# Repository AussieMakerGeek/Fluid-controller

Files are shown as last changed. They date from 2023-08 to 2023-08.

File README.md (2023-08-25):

# Fluid-controller
This is a fork of the original Fluid controller but it only retains handfulls of code and implements simple features for controlling my Gravoraph LS800 Co2 Laser that I converted using an MKS-Tinybee 

# Main functions
My implementation uses STM32 Bluepill over direct serial with the MKS-Tinybee using the new secondary serial function in FluidNC. I use the wifi function so bluetooth is not ideal for me, plus I can build this into my machine, no batteries etc.

# Display shows 
Machine coordinates, Work coordinates, Machine status, jog distance and whether X/Y jog or Z jog is active.  Since my machine has a visible laser, I also added a display for it's status.

Main functions of buttons: 
Home, Home Z, Unlock/Reset, Visible laser, Jog distance +, Jog distance -, directional buttons and Z/XY toggle.

No menus...

# Hardware
1. STM32 Bluepill (128k used, about 50% free)
2. ILI9341 based 2.5" display (320x240 res)
3. 11 X TTP223 Touch buttons - The Pad 'A' will need to be shorted to make them active LOW.

# Wiring
The buttons and display were directly wired to the Bluepill, no need for PCB. Mounted in a 3d Printed panel for install to the machine.

# Programming
Programming is done in Arduino IDE. All code exists in one single file. Button definitions set out the pins used.  

Project uses the TFT_eSPI library which requires setting the display parameters in user_setup.h in the library folder:
```
#define STM32
#define ILI9341_DRIVER
#define TFT_SPI_PORT
#define TFT_MOSI PA7
#define TFT_MISO PA6
#define TFT_SCLK PA5
define TFT_CS   PA4
#define TFT_DC   PA2
#define TFT_RST  PA3
#define LOAD_GFXFF
#define SMOOTH_FONT
#define SPI_FREQUENCY  55000000
#define SPI_READ_FREQUENCY  20000000 //Not used
```
It also uses the Multibutton library, but there is an issue in the library for STM32 - you need to eliminate the specific STM32 ifdef's (pinmode call) in PinButton.h or it will not compile.

# Panel
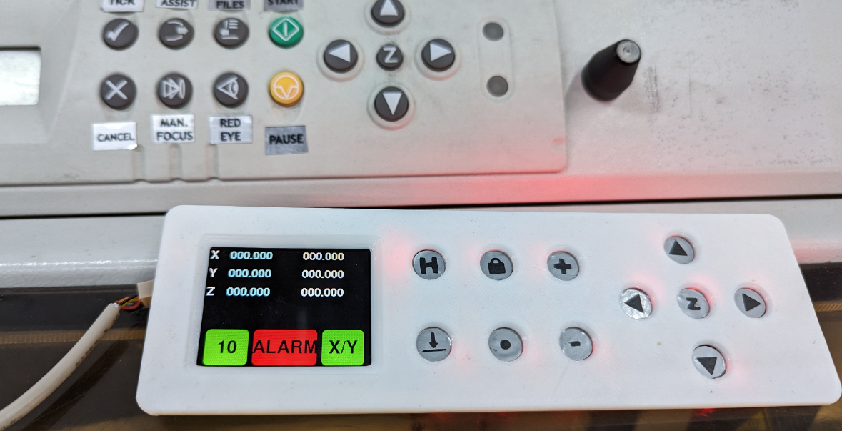
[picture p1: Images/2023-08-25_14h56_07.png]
Front

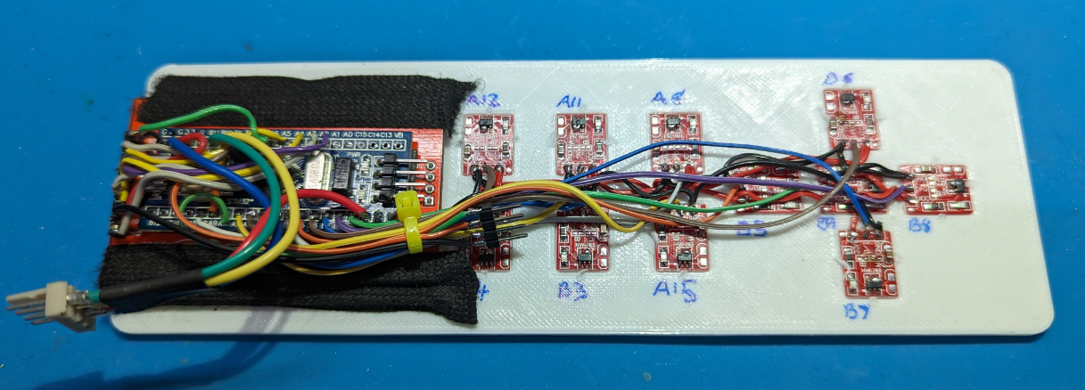
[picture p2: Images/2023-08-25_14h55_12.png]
Back

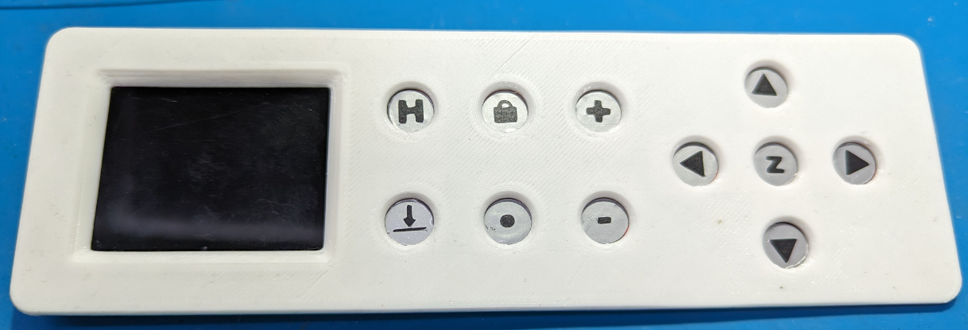
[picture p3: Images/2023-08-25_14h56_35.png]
Front2


See STL folder for printable file.

<!--
<img width="440" alt="pendantV2case_lid2" src="https://user-images.githubusercontent.com/20277013/214568520-32bf0ae3-2ae2-4814-8294-004ee3288210.png">
<img width="440" alt="pendantV2lid_case" src="https://user-images.githubusercontent.com/20277013/214570138-59b09fc4-4332-4c2e-8d71-3366ad1cf684.png">
-->

# Assembly
I just added all of the buttons to the panel and used my soldering iron to slightly melt the edges of the plastic to hold them in.  The LCD is held in place with some tape and the BluePill is secured to the back of it with some double sided tape.
I made some vinyl stickers to easily identify the button functions - They didn't turn out perfect but it'll do till my OCD takes over.

# How to operate
The functions are more specific to a Laser than a spindle CNC machine. Hence, the functions have been cut down.

* Directional controls - Move the gantry in the appropriate directions[^1]
* Pressing Z will swap to Z axis movement (only), press again to go back to X/Y mode
* Home Button - Issues $H command, for me, this is only X/Y
* Zhome - $HZ
* Unlock - Similar to the function from the original Fluid-Controller where it sends commands appropriate for the state of the machine to 'unlock' or otherwise 'resume' an Idle state.
* Laser - Issues a GRBL command to turn on a digital output.
* +/- - Increases or decreases the jog distance.

[^1]: Direction will need to be verified for your machine depending on origin etc.

# Other
Serial2 (PB11 / PB10) is used for communication with the machine, Serial(1) (PA9 / PA10) is used for debug output and is not required for operation.

FluidNC will need a line in the config file to enable the second serial terminal:

```
uart1:
  txd_pin: gpio.17
  rxd_pin: gpio.16
  baud: 115200
  mode: 8N1

uart_channel1:
  uart_num: 1
```
See http://wiki.fluidnc.com/en/config/uart_sections for more info

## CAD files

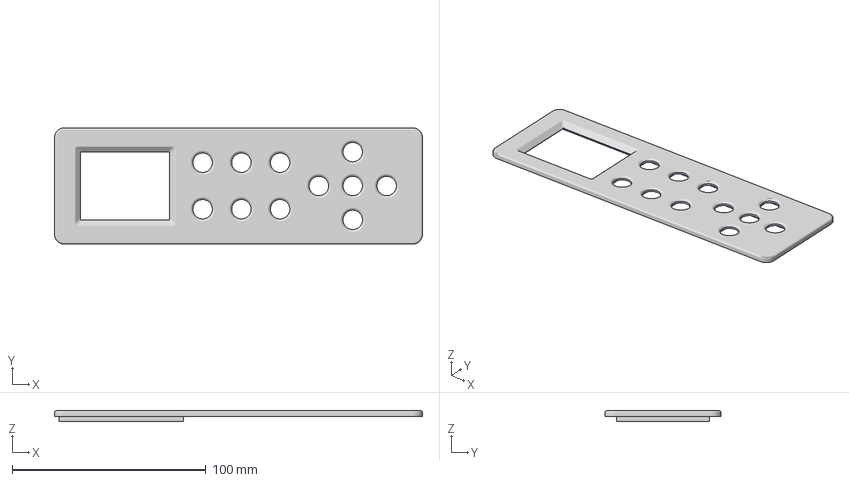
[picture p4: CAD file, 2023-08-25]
STL/Control Panel v1.3mf
190.0 x 60.0 x 5.50 mm

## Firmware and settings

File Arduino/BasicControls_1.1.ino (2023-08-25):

#include <PinButton.h>
#include <TFT_eSPI.h>      // Hardware-specific library

TFT_eSPI tft = TFT_eSPI(); // Invoke custom library

// Pin Defs
#define buttonPinUp PB7
#define buttonPinDn PB6
#define buttonPinLe PB5
#define buttonPinRt PB8
#define buttonPinOK PB9
#define buttonPinTL PB4
#define buttonPinTM PB3
#define buttonPinTR PA15
#define buttonPinBL PA12
#define buttonPinBM PA11
#define buttonPinBR PA8

//LCD Colours
#define TFT_LIGHTBLUE 0x86FF
#define TFT_LIGHTRED 0xF9E7
#define TFT_DARKBLUE 0x0018
#define TFT_OVERYELLOW 0xFF35
#define TFT_MEDIUMGREEN 0x04A2
#define TFT_DARKRED 0xA800
#define TFT_MEDIUMBLUE 0x3D5F
#define TFT_DARKORANGE 0xFAC0
#define TFT_LEFT    1
#define TFT_CENTER  2
#define TFT_RIGHT   3
#define TFT_TRANSP  true
#define TFT_OBLQ  false

#define MAX_JOGSTR 50
#define MAX_STATUSSTR 50
#define LINEHEIGHT_DEF  40

enum machinestate {
  Unknwn,
  Alarm,
  Idle,
  Jog,
  Home,
  Check,
  Run,
  Cycle,
  Hold,
  Door,
  Sleep
};

PinButton buttonUp(buttonPinUp);
PinButton buttonDn(buttonPinDn);
PinButton buttonLe(buttonPinLe);
PinButton buttonRt(buttonPinRt);
PinButton buttonOK(buttonPinOK);
PinButton buttonTL(buttonPinTL);
PinButton buttonTM(buttonPinTM);
PinButton buttonTR(buttonPinTR);
PinButton buttonBL(buttonPinBL);
PinButton buttonBM(buttonPinBM);
PinButton buttonBR(buttonPinBR);

HardwareSerial Serial2(PB11, PB10);

static char mStateStr[][11] { "? ?", "ALM", "IDLE", "JOG", "HOME", "CHECK", "RUN", "CYCLE", "HOLD", "DOOR", "SLEEP" };
char jogStr[MAX_JOGSTR];
char statusStr[MAX_STATUSSTR];
char sbuf[20];
float mX, mY, mZ;  //Machine positions
float wX, wY, wZ;  //Work positions

float lastXPos = 0.1, lastYPos = 0.1, lastZPos = 0.1;
float lastXwPos = 0.1, lastYwPos = 0.1, lastZwPos = 0.1;

unsigned long sinceStart, lastGrblState;
int jogDistance[] = {1,5,10,50,100,200};
int jogIndex = 2;
bool zJog = 0;
bool laserStatus = 0;
const int updateInterval = 198;
bool doorValue = 1;
bool lastDoorValue = 0;

bool doorUpdated = false;
bool xyUpdated = true;
bool jogUpdated = true;

String grblState;
machinestate mState = Unknwn;
machinestate lastmState = Idle;

//************************************
// Functions
//************************************

void printAxisCoords(float m, float w, byte row) {
  tft.fillRect(35, row * LINEHEIGHT_DEF + 2, 285, LINEHEIGHT_DEF, TFT_BLACK); //clear to eol
  if (m > 0) tftPrint(TFT_LEFT, TFT_TRANSP, TFT_LIGHTBLUE, TFT_BLACK, 25, row * LINEHEIGHT_DEF, 0, "+");
  else if (m < 0) tftPrint(TFT_LEFT, TFT_TRANSP, TFT_LIGHTBLUE, TFT_BLACK, 25, row * LINEHEIGHT_DEF, 0, "-");
  sprintf(sbuf, "%03d.%03d", (int)abs(m) % 1000, (int)(fabsf(m) * 1000) % 1000);
  tftPrint(TFT_LEFT, TFT_TRANSP, TFT_LIGHTBLUE, TFT_BLACK, 40, row * LINEHEIGHT_DEF + 2, 0, sbuf);
  if (w > 0) tftPrint(TFT_LEFT, TFT_TRANSP, TFT_WHITE, TFT_BLACK, 170, row * LINEHEIGHT_DEF, 0, "+");
  else if (w < 0) tftPrint(TFT_LEFT, TFT_TRANSP, TFT_WHITE, TFT_BLACK, 170, row * LINEHEIGHT_DEF, 0, "-");
  sprintf(sbuf, "%03d.%03d", (int)abs(w) % 1000, (int)(fabsf(w) * 1000) % 1000);
  tftPrint(TFT_LEFT, TFT_TRANSP, TFT_WHITE, TFT_BLACK, 185, row * LINEHEIGHT_DEF + 2, 0, sbuf);
}

void tftUpdate(bool active) {
  if(active){ // Only bother if machines is not idle
    if (lastXPos != mX || lastXwPos != wX){ //Only update if the values have changed
      tftPrint(TFT_LEFT, TFT_TRANSP, TFT_WHITE, TFT_BLACK, 2, 0 * LINEHEIGHT_DEF + 2, 0, "X");
      printAxisCoords(mX, mX - wX, 0);
      lastXPos = mX;
      lastXwPos = wX;
    }
    if (lastYPos != mY || lastYwPos != wY){
      tftPrint(TFT_LEFT, TFT_TRANSP, TFT_WHITE, TFT_BLACK, 2, 1 * LINEHEIGHT_DEF + 2, 0, "Y");
      printAxisCoords(mY, mY - wY, 1);
      lastYPos = mY;
      lastYwPos = wY;
    }
    if (lastZPos != mZ || lastZwPos != wZ){
      tftPrint(TFT_LEFT, TFT_TRANSP, TFT_WHITE, TFT_BLACK, 2, 2 * LINEHEIGHT_DEF + 2, 0, "Z");
      printAxisCoords(mZ, mZ - wZ, 2);
      lastZPos = mZ;
      lastZwPos = wZ;
    }
  }
  sprintf(sbuf, "%s", mStateStr[mState]);

  if (mState == Door){
    if (lastDoorValue != doorValue){
      if (doorValue == 0){
        tftPrintBig(TFT_ORANGE, TFT_BLACK, 160, 220, 120, sbuf); // Flag to resume
      }else{
        tftPrintBig(TFT_DARKRED, TFT_BLACK, 160, 220, 120, sbuf); //Halted
      }
      lastDoorValue = doorValue;
    }
  } 

  if(lastmState != mState){
    if (mState == Alarm || mState == Unknwn)
      tftPrintBig(TFT_DARKRED, TFT_BLACK, 160, 220, 120, sbuf);
    else if (mState == Hold)
      tftPrintBig(TFT_ORANGE, TFT_BLACK, 160, 220, 120, sbuf);
    else if (mState == Run || mState == Jog)
      tftPrintBig(TFT_BLACK, TFT_ORANGE, 160, 220, 120, sbuf);
    else if (mState != Door) tftPrintBig(TFT_BLACK, TFT_MEDIUMGREEN, 160, 220, 120, sbuf);
    lastmState = mState;
  }
  
  // Only update when needed.
  if (jogUpdated == true){
    tftPrintBig(TFT_MEDIUMGREEN, TFT_BLACK, 50, 220, 80, String(jogDistance[jogIndex]));
    jogUpdated = false;
  }
  if (xyUpdated == true){
    if (zJog == 0){
        tftPrintBig(TFT_MEDIUMGREEN, TFT_BLACK, 270, 220, 80, "X/Y");
        xyUpdated = false;
    }else{
      tftPrintBig(TFT_DARKORANGE, TFT_BLACK, 270, 220, 80, "Z");
      xyUpdated = false;
    }
  }
}

void tftPrint(int align, bool transp, int fg, int bg, byte col, byte row, byte len, String txt) {
  //tft.setFreeFont(&FreeSans9pt7b);
  tft.setFreeFont(&FreeSansBold12pt7b);
  if (transp) tft.setTextColor(fg);
  else {
    tft.setTextColor(fg, bg);
    if (align == TFT_RIGHT) {
      if (len) tft.fillRect(col - len, row, len, LINEHEIGHT_DEF, TFT_BLACK);
      tft.setTextDatum(TR_DATUM);
    }
    else if (align == TFT_CENTER) {
      if (len) tft.fillRect(col - len / 2, row, len, LINEHEIGHT_DEF, TFT_BLACK);
      tft.setTextDatum(MC_DATUM);
    }
    else {
      if (len) tft.fillRect(col, row, len, LINEHEIGHT_DEF, TFT_BLACK);
      tft.setTextDatum(TL_DATUM);
    }
  }
  tft.drawString(txt, col, row);
  tft.setTextDatum(TL_DATUM);
}

void tftPrintBig(int bg, int fg, int col, int row, int len, String txt) {
  tft.setTextDatum(MC_DATUM);
  //tft.fillRect(col - len / 2, row - LINEHEIGHT_DEF - 10, len, 2 * LINEHEIGHT_DEF - 10 , bg);
  tft.fillSmoothRoundRect(col - (len / 2), row - LINEHEIGHT_DEF - 10, len, 2 * LINEHEIGHT_DEF - 10 , 8,bg,TFT_BLACK);
  //                         255-110/2,
  tft.setTextColor(fg);
  tft.setFreeFont(&FreeSansBold18pt7b);
  tft.drawString(txt, col, row - 17);
  tft.setTextDatum(TL_DATUM);
}
void tftPrintColor(int color, byte col, byte row, String txt) {
  tftPrint(TFT_LEFT, TFT_OBLQ, color, TFT_BLACK, col, row, 0, txt);  
}

void tftPrintSimple(byte col, byte row, String txt) {
  tftPrint(TFT_LEFT, TFT_OBLQ, TFT_WHITE, TFT_BLACK, col, row, 0, txt);
}

void getGrblState(bool full) {
  char a;
  Serial2.write('?');
  grblState = "";
  while (Serial2.available()) {
    a = Serial2.read();
    Serial.write(a);
    if (a == '\n') {
      if (grblState.indexOf("<") >= 0) {
        grblState.remove(0, grblState.indexOf("<"));
        //Serial.println(grblState);
        if (grblState.charAt(1) == 'J') mState = Jog;
        else if (grblState.charAt(3) == 'm') mState = Home;
        else if (grblState.charAt(4) == 'd') mState = Hold;

        // Handle the door state
        else if (grblState.charAt(1) == 'D'){
           mState = Door; //Door is open
           if (grblState.charAt(6) == '0'){
             doorValue = 0; //Door was opened but is now close
           }else{
             doorValue = 1; //Door is open
           }
        }
        else if (grblState.charAt(1) == 'R') mState = Run;
        else if (grblState.charAt(1) == 'A') mState = Alarm;
        else if (grblState.charAt(1) == 'I') mState = Idle;
        else mState = Unknwn;
        if (full) {
          if (grblState.indexOf("MPos:") >= 0) {
            grblState.remove(0, grblState.indexOf("MPos:") + 5);
            convertPos(true, grblState);
          }
          if (grblState.indexOf("|FS:") >= 0) {
            grblState.remove(0, grblState.indexOf("|FS:") + 4);
            grblState.remove(0, grblState.indexOf(",") + 1);
            //reportedSpindleSpeed = grblState.toInt();
          }
          if (grblState.indexOf("WCO:") >= 0) {
            grblState.remove(0, grblState.indexOf("WCO:") + 4);
            convertPos(false, grblState);
          }
          else if (grblState.indexOf("|Ov:") >= 0) {
            grblState.remove(0, grblState.indexOf("|Ov:") + 4);
            //convertOverride(grblState);
            if (grblState.indexOf("|A:") >= 0) {
              grblState.remove(0, grblState.indexOf("|A:") + 3);
            }
          }
        }
      }
    } else {
      grblState.concat(a);
    }
  }
  lastGrblState = sinceStart;
}

void convertPos(bool isM, String s) {
  // Serial.println(s);
  static float x, y, z;
  x = s.substring(0, s.indexOf(",")).toFloat();
  s.remove(0, s.indexOf(",") + 1);
  y = s.substring(0, s.indexOf(",")).toFloat();
  s.remove(0, s.indexOf(",") + 1);
  if (s.indexOf("|") < 7) {
    z = s.substring(0, s.indexOf("|")).toFloat();
  } else {
    z = s.substring(0, s.indexOf(">")).toFloat();
  }
  if (isM) {
    mX = x;
    mY = y;
    mZ = z;
  } else {
    wX = x;
    wY = y;
    wZ = z;
  }
}

void forceEndJog() {
  Serial.println("C");
  Serial2.write(0x85);
  //  Serial.println("cancel");
  delay(100);
  getGrblState(false);
  while (mState == Jog) {
    Serial.println("D");
    Serial2.write(0x85);
    //    Serial.println("cancel");
    delay(100);
    getGrblState(true);
  }
}

void waitEndJog() {
  getGrblState(false);
  while (mState == Jog) {
    delay(100);
    getGrblState(true);
    //    Serial.print("jog wait...");
    //    Serial.println(mState);
  }
}

//************************************
// End of Functions
//************************************


void setup() {
  Serial.begin(115200);
  Serial2.begin(115200);
  tft.init();
  tft.setRotation(3);
  tft.fillScreen(TFT_BLACK);
  grblState.reserve(100);
  getGrblState(false);
  Serial.println("Init...");
  tftUpdate(true);
  delay(2000); //Wait for the buttons to settle
}

void loop() {
  sinceStart = millis() + 1000;
  if (sinceStart - lastGrblState > updateInterval) {
    if (mState != Alarm && mState != Idle && mState != Unknwn && mState != Door){
      getGrblState(true); //Machine is doing something
      tftUpdate(true); //Update full details
    }else{
      getGrblState(false); // Machine is idle, just get status
      tftUpdate(false); //Just update status
    }
  }
  buttonUp.update();
  buttonDn.update();
  buttonLe.update();
  buttonRt.update();
  buttonOK.update();
  buttonTL.update();
  buttonTM.update();
  buttonTR.update();
  buttonBL.update();
  buttonBM.update();
  buttonBR.update();

  if(buttonTL.isClick()){
    //Home
    Serial2.println((char *)"$H");
  }
  
  if(buttonBL.isClick()){
    //Home Z Azis
    Serial2.println((char *)"$HZ");
  }
  
  if(buttonTM.isClick()){
    if(mState == Alarm){ 
      Serial2.println((char *)"$X"); //Unlock
    }
      else if (mState == Run) Serial2.write('!');
      else if (mState == Hold) Serial2.write('~');
      else if (mState == Door && doorValue == 0){ //No point unless door is now closed.
        Serial2.write('~');
      } 
  }
  
  if(buttonBM.isClick()){
    if (laserStatus == 0){
      Serial2.println((char *)"M62 P0");
      laserStatus = 1;
      //tft.drawLine(310,5,310, )
      tft.drawWideLine(300, 5, 300, 80, 3, TFT_DARKRED, TFT_BLACK);
      tft.fillCircle(300, 80, 7, TFT_DARKRED);
    }else{
      Serial2.println((char *)"M63 P0");
      laserStatus = 0;
      tft.fillRect(293, 5, 15, 90, TFT_BLACK);
    }
  }

  if(buttonTR.isClick()){
    if (jogIndex<5){
      jogIndex++;
      jogUpdated = true;
      //tftPrintBig(TFT_MEDIUMGREEN, TFT_BLACK, 50, 220, 80, String(jogDistance[jogIndex]));
    }
  }

  if(buttonBR.isClick()){
    if (jogIndex>0){
      jogIndex--;
      jogUpdated = true;
      //tftPrintBig(TFT_MEDIUMGREEN, TFT_BLACK, 50, 220, 80, String(jogDistance[jogIndex]));
    }
  }

  if(buttonUp.isClick()){
    if (zJog == 0){ // Jog Y Axis
      int dist = jogDistance[jogIndex];
      snprintf(jogStr, MAX_JOGSTR, "$J=G21G91X0Y%dZ0F%d", dist, 3000);
    }else{ // Jog Z Axis
      int dist = -1 * jogDistance[jogIndex];
      snprintf(jogStr, MAX_JOGSTR, "$J=G21G91X0Y0Z%dF%d", dist, 1000);
    }
    Serial2.println(jogStr);
    Serial.println(jogStr);
  }
  if(buttonDn.isClick()){
    if (zJog == 0){ // Jog Y Axis
      int dist = -1 * jogDistance[jogIndex];
      snprintf(jogStr, MAX_JOGSTR, "$J=G21G91X0Y%dZ0F%d", dist, 3000);
    }else{
      int dist = jogDistance[jogIndex];
      snprintf(jogStr, MAX_JOGSTR, "$J=G21G91X0Y0Z%dF%d", dist, 1000);
    }
    Serial2.println(jogStr);
    Serial.println(jogStr);
  }
  if(buttonLe.isClick()){
    if (zJog == 0){  // Only Jog if Z is not enabled
      int dist = -1 * jogDistance[jogIndex];
      snprintf(jogStr, MAX_JOGSTR, "$J=G21G91X%dY0Z0F%d", dist, 3000);
      Serial2.println(jogStr);
      Serial.println(jogStr);
    }
  }
  if(buttonRt.isClick()){
    if (zJog == 0){ // Only Jog if Z is not enabled
      int dist = jogDistance[jogIndex];
      snprintf(jogStr, MAX_JOGSTR, "$J=G21G91X%dY0Z0F%d", dist, 3000);
      Serial2.println(jogStr);
      Serial.println(jogStr);
    }
  }
  if(buttonOK.isClick()){
    if (zJog == 0){
      zJog = 1;
      //tftPrintBig(TFT_DARKORANGE, TFT_BLACK, 270, 220, 80, "Z");
      xyUpdated = true;
    }else{
      zJog = 0;
      //tftPrintBig(TFT_MEDIUMGREEN, TFT_BLACK, 270, 220, 80, "X/Y");
      xyUpdated = true;
    }
  }
}
